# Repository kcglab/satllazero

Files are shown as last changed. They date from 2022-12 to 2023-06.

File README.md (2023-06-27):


DOI (https://doi.org/10.21105/joss.05147)

# Overview
**SATLLA-0**, also known as satllazero, is an open-source project that aims to develop a fully functional pico-satellite. The project includes both the software and hardware of the pico satellite, as well as a ground station. The goal of the project is to enable any science class (in high school or university) to experience the "new space" at a fraction of the price of existing solutions.

# Our Vision
The SATLLA-0 project is all about building a fully functional pico-satellite that's based on a design that's already been launched into space (see [SATLLA-2B](https://tinygs.com/satellite/SATLLA-2B)). Researchers and 12K students can get involved, and the project includes the software, hardware, and ground station you need to make it happen. The goal is to make it possible for any science class to experience the "new space" without breaking the bank.

<div style="display: flex; justify-content: center;">
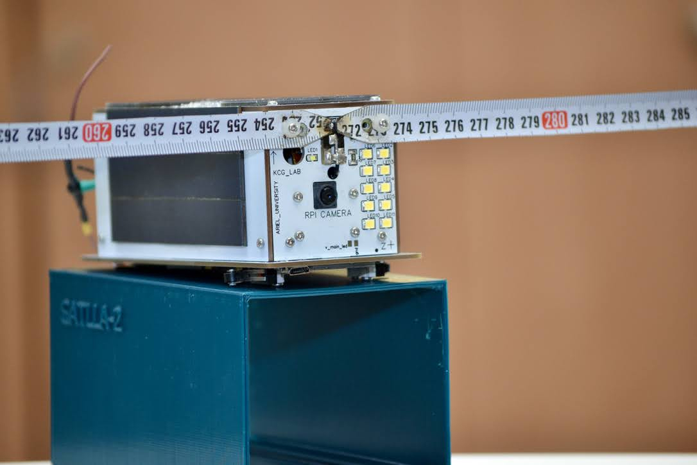
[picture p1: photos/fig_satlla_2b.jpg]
SATLLA-2B
  
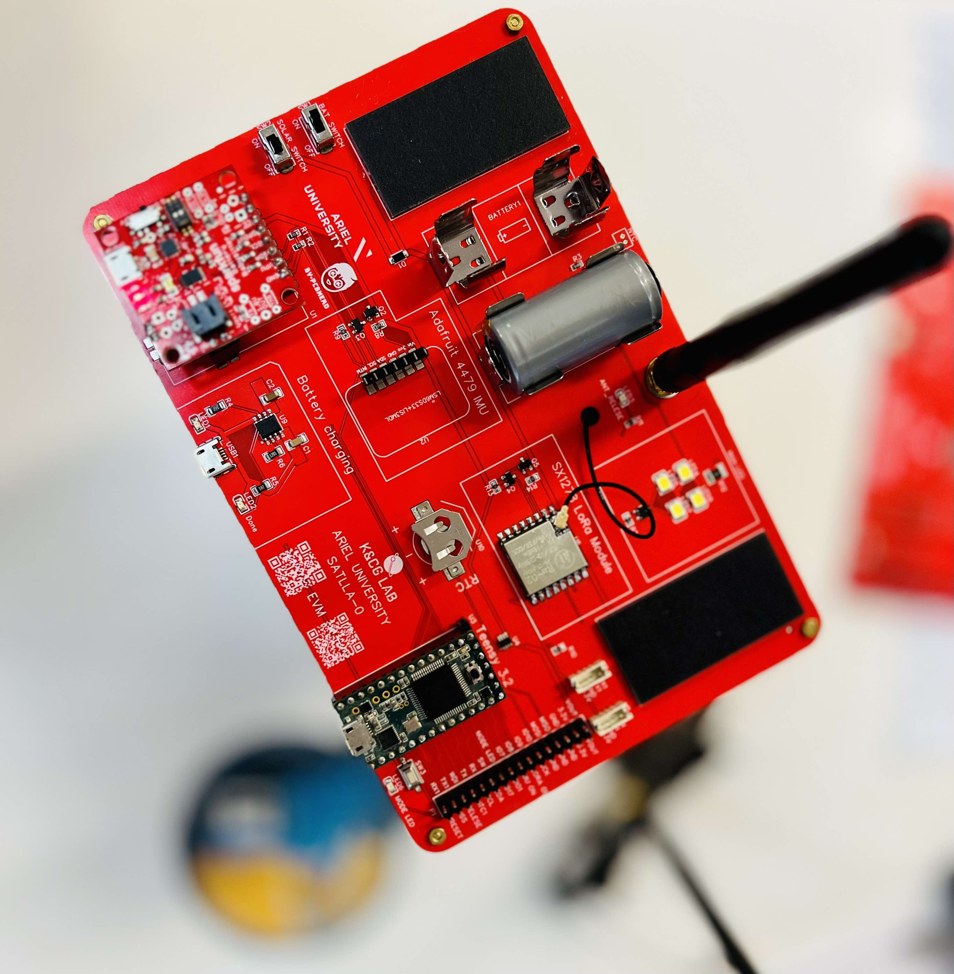
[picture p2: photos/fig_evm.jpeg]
SATLLA-0 EVM Board
  
</div>

## Table of contents

- [Description](#description)
- [What's included](#whats-included)
- [Features](#features)
- [Features](#Features)
- [Supported Hardware](#supported-Hardware)
- [SATLLA-0 EVM Board](#satlla-0-evm-board)
- [Installation](#installation)
- [For more info](#for-more-info)
- [Bugs and feature requests](#bugs-and-feature-requests)
- [Copyright and license](#copyright-and-license)
- [Links](#links)
- [Citation](#citation)

## Description
The SATLLA-0 core flight system is an open-source flight software that is used by the SATLLA-2B satellite. The library was designed to be a starting point for academic institutions and schools that want to build or experiment with a laboratory or functional nanosatellite. The system has three main components: the Master, the on-board computer, and the Ground Station. For more information on each component, please see the following section. The main library contains the satellite's flight software, written in Arduino. Arduino is a C/C++ based programming language that is open source and easy to learn. This library was developed for the Teensy 3.x/4.x microcontroller family, which is the main microprocessor unit (MPU) of the SATLLA-2B nanosatellite. However, the library can be compiled for other microcontrollers using the definitions available in the library.

## What's included
The repo is structured as follows:
+ software: The flight software is divided into three sub-folders:
  + SAT0_Ground: The ground station module written in Arduino [SAT0_Ground](/software/SAT0_Ground).
  + SAT0_Master: The satellite main computer module written in Arduino [SAT0_Master](/software/SAT0_Master)
  + SAT0_OBC: The on-board computer (OBC) module written in Python [SAT0_OBC](/software/SAT0_OBC).
+ hardware: Contains the hardware schematics of the satellite.
+ MD: Contains MD files describing the satellite commands, beacons and bill of materials (BOM).
+ stl: Contains 3D sketches.
+ paper: Contains the JOSS submission paper.

The SATLLA-0 libraries offer the ability to be used independently, meaning that each library component may be utilized separately according to the user's specific requirements. For instance, the SAT0_MASTER satellite flight software can be integrated with alternate ground station software. However, it is essential to know that adjustments relating to radio frequencies and message structures are needed.

## Features
The SATLLA-0 flight software platform includes the following key features:
+ A functional nanosatellite based on a Teansy microcontroller which supports the following subsystems: 
  + 2P structure.
  + Electrical Power System (EPS).
  + Telecommand and communications based on LoRa UHF and S-band. 
  + GPS.
  + Inertial Measurement Unit (IMU).
  + Thermistors (Temperature).
  + High-power array LED.
+ An on-board computer (OBC) for research activities based on a RaspberryPi Zerro.
  + Linux-based 
  + Integrated camera.
  + Variety of payloads including Attitude Determination and Control System (ADCS) based on reaction wheels, an Automatic Dependent Surveillance-Broadcast (ADS-B) receiver for surveillance aircraft.
+ A functional ground station based on an ESP32 board.

## Supported Hardware
A list of all the hardware required to assemble a functional nanosatellite is available [here](/MD/bom.MD).
The following boards are being used in this repository:
+ SAT0_Ground: WiFi LoRa ESP32 from Heltec or TTGO.
+ SAT0_Master: Teensy 3.6/4.1 microcontroller.
+ SAT0_OBC: RPI-Zero or RPI-Zero-W.

## SATLLA-0 EVM Board
The SATLLA-0 evaluation board is specifically designed for flat CubeSats, offering a comprehensive platform for testing and experimenting with various satellite functionalities. This evaluation board incorporates a wide range of satellite sensors, enabling researchers and engineers to assess and explore the full capabilities of the SATLLA-0 system. By providing access to most of the essential sensors used in satellites, the board allows for in-depth evaluation and analysis of different aspects, such as thermal management, power optimization, and communication protocols.
Please refer to [EVM_BOARD](/hardware/evm_board) for more details.

## Installation
SATLLA-0 is written in Arduino, and can be installed via Arduino, Teensyduino or any other IDE supporting Arduino.
Please refer to [wiki](https://github.com/kcglab/satllazero/wiki) for details installation.

## For more info
For more into on SATLLA-0, its workings, inputs, outputs and more see the [wiki](https://github.com/kcglab/satllazero/wiki).

## Bugs and feature requests
Please submit bug reports and feature requests to the issue tracker on GitHub: [SATLLA-0 issue tracker](https://github.com/kcglab/satllazero/issues)

## Copyright and license
This program is released as open source software under the terms of [GPL3 License](https://github.com/kcglab/satllazero/blob/main/LICENSE).

## Links
1. A great place to learn more on SATLLA project: [SATLLA Channel](https://www.youtube.com/watch?v=bJ7NgBDLjMQ)
2. SATLLA 2 DIY KIT Assembly [iFixIt Build Instructions](https://www.ifixit.com/Guide/SATLLA+2+DIY+KIT+Assembly/147004)
3. A good starting point is to use a Weather Balloons: [Extreme Long-RAnge Wi-Fi](https://www.youtube.com/watch?v=0xc7XjHUJkM&t=41s)

## Citation
If you'd like to cite us in a project or publication, please include a reference to the JOSS paper:
```
@article{Ronen_SATLLA0_A_Flight_2023,
  author = {Ronen, Rony and Britvin, Michael and Moshe, Boaz Ben},
  doi = {10.21105/joss.05147},
  journal = {Journal of Open Source Software},
  month = jun,
  number = {86},
  pages = {5147},
  title = {{SATLLA0: A Flight Software Platform for Aerospace and STEM Education}},
  url = {https://joss.theoj.org/papers/10.21105/joss.05147},
  volume = {8},
  year = {2023}
}
```

Ariel University. 2023.

## Troubleshoot
* Issue w/Actions

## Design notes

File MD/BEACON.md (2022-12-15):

# SATLLA0 Decode Long Beacon:

## Description:
SATLLA0 has long and short beacons. Each beacon is sent in a period of 45 seconds to 1 minute depends on the battery power.

## Short Beacon:
- Short beacon consists of 12  bytes:
> uint8_t local_address;   // 1, SAT Address/Call Sign \
> uint8_t sd_outbox;       // 2, Pending files to sent \
> uint8_t msg_type;        // 3, Message Type per messgae_type_e enum \
> uint8_t msg_received;    // 4, Recevied Messages \
> uint16_t msg_index;      // 5, Message ID \
> uint16_t battery_volts;  // 6, Read battery voltage (mV) \
> int16_t battery_current; // 7, Read average current (mA) \
> int8_t sns_ntc1;         // 8, Temperature \
> int8_t sns_ntc2;         // 9, Temperature \

## Long Beacon:
- Long beacon consists of a header (9 bytes) and payload (dynamic size).
- The type of the beacon located in the 3rd byte of the message.
- SATLLA0 has messages that aren't beacons. Nevertheless, all of them has the same structure: 9 byte header and rest is payload.
- The header is as follows:
- lora_data_t:
> uint8_t local_address; // 1, SAT Address/Call Sign. \
> uint8_t destination;   // 2, Ground Station address \
> uint8_t msg_type;      // 3, Message Type per messgae_type_e enum \ 
> uint8_t msg_size;      // 4, Message Length (for payload) \
> uint16_t msg_index;    // 5, Message ID \
> uint16_t msg_time;     // 7, The time of the message since last boot \
> uint8_t msg_ack_req;   // 9. Message ack req. 0=False. 1=True \
> uint8_t msg_payload[]; // 10. The Data \

- The payload structure in a long beacon consists of 52 bytes as follows:
-- gps_data_t (include date_time_t) 20 bytes
-- sns_data_t 16 bytes
-- battery_data_t 12 bytes
-- sd_data_t 4 bytes

- gps_data_t:
> date_time_t gps_date_time; // 1, Date/Time \
> float gps_lat;        // 2, Latitude \
> float gps_lng;        // 3, Longitude \
> uint16_t gps_alt;     // 4, Altitude \
> uint16_t gps_speed;   // 5, Sat Speed KPH \
> uint16_t gps_course;  // 6, Sat Course Degree \
> uint8_t gps_sat;      // 7, Number of gps satellites \

-date_time_t:
> uint8_t gps_month; // 1, Month \
> uint8_t gps_day;   // 2, Day \
> uint8_t gps_hour;  // 3, Hour \
> uint8_t gps_min;   // 4, Min \

- sns_data_t:
> int16_t sns_gx;         // 1, Gyro X rad/s \
> int16_t sns_gy;         // 2, Gyro Y rad/s \
> int16_t sns_gz;         // 3, Gyro Z rad/s \
> int16_t sns_mx;         // 4, Mag X uTesla \
> int16_t sns_my;         // 5, Mag Y uTesla \
> int16_t sns_mz;         // 6, Mag Z uTesla \
> int16_t sns_bmp_temp_c; // 7, Temperature C \
> int8_t sns_ntc1;        // 8, ? Temperature 1 C \
> int8_t sns_ntc2;        // 9, ? Temperature 2 C \

- battery_data_t
> int8_t battery_soc;             // 1, Read state-of-charge (%) \
> int8_t battery_health;          // 2, Read state-of-health (%) \
> uint16_t battery_volts;         // 3, Read battery voltage (mV) \
> int16_t battery_current;        // 4, Read average current (mA) \
> uint16_t battery_full_capacity; // 5, Read full capacity (mAh) \
> uint16_t battery_capacity;      // 6, Read remaining capacity (mAh) \
> int16_t battery_power;          // 7, Read average power draw (mW) \

- sd_data_t:
> uint8_t sd_outbox; // 1, Pending files to upload \
> uint8_t sd_sent;   // 2, Files sent \
> uint8_t sd_rpi;    // 3, Pending files under Mission Computer to upload \
> uint8_t sd_files;  // 4, All files on the SD - Informative. \

- enum messgae_type_e:
> type_becon = 0x00 \
> type_echo = 0x01 \
> type_ack = 0x02 \
> type_range = 0x03 \
> type_rpi = 0x04 \
> type_text = 0x05 \
> type_sbeacon = 0x06 \
> type_command = 0x07 \
> type_setting = 0x08 \
> type_none = 0x09 \
> type_mv = 0x0A \
> type_ld = 0x0B \
> type_rng = 0x0C \

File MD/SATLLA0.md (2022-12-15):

# SATLLA0 Code

## 1. Setup
- 1.1 RTC
- 1.2 SPI Pin: 13 or 14 (Based on Teensy)
- 1.3 Wire
- 1.4 Watchdog
- 1.5 SD Card
- 1.6 Flash FS
- 1.7 Mode Led
- 1.8 Main LED
- 1.9 Laser Setup
- 1.10 EEPROM
- 1.11 IMU (BNO or LSM)
- 1.12 LoRa 433
- 1.13 LoRa 2.4
- 1.14 GPS
- 1.15 NTC (1 and 2)
- 1.16 Babysitter (BQ27441)
- 1.17 Initial Boot (Antenna Deploy)
- 1.18 Increase Reset index

## 2. Main Loop
- 2.1 WD Heartbeat
- 2.2 Read Babysitter Func
- 2.3 Check Battery Status Func 
- 2.4 Set satellite mode Func (Based on battery status)
- 2.5 If state is higher than panic, then:
- 2.5.1 If 1 minute passed from last beacon, then:
- 2.5.1.1 Set Short/Long beacon (Based on battery status and at least 5 long every hour)
- 2.5.1.2 Prepare Beacon parameters Func
- 2.5.1.3 Send Beacon using LoRa 433
- 2.5.1.4 Wait one second
- 2.5.1.5 Send Beacon using LoRa 2.4 (If loRa 2.4 is On - Depends on Satellite health)
- 2.6 Smart wait for 20 seconds (Listen to commands)
- 2.7 Handle Tasks Func (Auto and based on commands received)
- 2.8 If not in mission
- 2.8.1 If GFSK is allowed and state is higher than panic, then:
- 2.8.1.1 Switch modem to GFSK 433
- 2.8.1.2 Send beacon using GFSK 433
- 2.8.1.3 Switch back to LoRa 433
- 2.8.2 If in panic mode, then
- 2.8.2.1 Sleep for 45 seconds
- 2.8.2.2 Else, Sleep for at most 15 seconds (Depends on last beacon sent time)

## 3. Smart Delay Func
- 3.1 Loop for period
- 3.1.1 If GPS is on, feed GPS
- 3.1.2 If received 433, break
- 3.1.3 If received 2.4, break
- 3.1.4 WD Heartbeat
- 3.2 If break, handle message (2.4 or 433)
- 3.3 If restart requested, wait 2 seconds and restart.

## 4. Sleep Delay Func
- 4.1 Loop for period
- 4.1.1 If IMU is On and Not Sleep, Sleep
- 4.1.2 If LoRa 433 is On and Not Sleep, Sleep
- 4.1.3 If Lora 2.4 is On and Not Sleep, Sleep
- 4.1.4 If GPS is On and Not Sleep, Sleep
- 4.1.5 WD Heartbeat
- 4.2.1 If IMU is On and Sleep, Resume
- 4.2.2 If LoRa 433 is On and Sleep, Resume
- 4.2.3 If Lora 2.4 is On and Sleep, Resume
- 4.2.3 If GPS is On and Sleep, Resume
- 4.1.6 WD Heartbeat

## 5. Satellite Health Func
- 5.1 Switch Satellite State
- 5.1.2 Case: Panic power
- 5.1.2.1 If GPS is On, then turn Off
- 5.1.2.2 If IMU is On, then turn Off
- 5.1.2.4 If LoRa 433 is On, then turn Off
- 5.1.2.5 If LoRa 24 is On, then turn Off
- 5.1.3 Case: Medium power
- 5.1.3.1 If GPS is On, then turn Off
- 5.1.3.2 If IMU is Off, then turn On
- 5.1.3.4 If LoRa 433 is Off, then turn On
- 5.1.3.5 If LoRa 24 is Off, then turn On
- 5.1.3 Case: High power
- 5.1.3.1 If GPS is Off, then turn On
- 5.1.3.2 If IMU is Off, then turn On
- 5.1.3.4 If LoRa 433 is Off, then turn On
- 5.1.3.5 If LoRa 24 is Off, then turn On

## 6. Switch Beacon Type Func
- 6.1 If Satellite state > Medium power, then
- 6.1.2 Use Long Beacon
- 6.1.3 Else, Use Short Beacon
- 6.1.4 In addition, If last sent long beacon > 1 hour, then 
- 6.1.4.1 Use Long Beacon for the next 5 messages

## 7. Handle Beacon Func:
- 7.1 Read Babysitter
- 7.2 Read IMU
- 7.3 Read NTC
- 7.4 Read GPS
- 7.5 If SD, then list files
- 7.6 If SD error or SD overwrite, then list files from FS
- 7.7 Add Infodata to beacon
- 7.8 Add Metadata to beacon 
- 7.9 Prepare Long/Short beacon

## 8. Send Beacon Func:
- 8.1 If Stop Flag raised, return
- 8.2 Send Short/Long beacon via LoRa 433/24
=======
1.1 RTC
1.2 SPI Pin: 13 or 14 (Based on Teensy)
1.3 Wire
1.4 Watchdog
1.5 SD Card
1.6 Flash FS
1.7 Mode Led
1.8 Main LED
1.9 Laser Setup
1.10 EEPROM
1.11 IMU (BNO or LSM)
1.12 LoRa 433
1.13 LoRa 2.4
1.14 GPS
1.15 NTC (1 and 2)
1.16 Babysitter (BQ27441)
1.17 Initial Boot (Antenna Deploy)
1.18 Increase Reset index

## 2. Main Loop
2.1 WD Heartbeat
2.2 Read Babysitter Func
2.3 Check Battery Status Func 
2.4 Set satellite mode Func (Based on battery status)
2.5 If state is higher than panic, then:
2.5.1 If 1 minute passed from last beacon, then:
2.5.1.1 Set Short/Long beacon (Based on battery status and at least 5 long every hour)
2.5.1.2 Prepare Beacon parameters Func
2.5.1.3 Send Beacon using LoRa 433
2.5.1.4 Wait one second
2.5.1.5 Send Beacon using LoRa 2.4 (If loRa 2.4 is On - Depends on Satellite health)
2.6 Smart wait for 20 seconds (Listen to commands)
2.7 Handle Tasks Func (Auto and based on commands received)
2.8 If not in mission
2.8.1 If GFSK is allowed and state is higher than panic, then:
2.8.1.1 Switch modem to GFSK 433
2.8.1.2 Send beacon using GFSK 433
2.8.1.3 Switch back to LoRa 433
2.8.2 If in panic mode, then
2.8.2.1 Sleep for 45 seconds
2.8.2.2 Else, Sleep for at most 15 seconds (Depends on last beacon sent time)

## 3. Smart Delay Func
3.1 Loop for period
3.1.1 If GPS is on, feed GPS
3.1.2 If received 433, break
3.1.3 If received 2.4, break
3.1.4 WD Heartbeat
3.2 If broken, handle message (2.4 or 433)
3.3 If restart requested, wait 2 seconds and restart.

## 4. Sleep Delay Func
4.1 Loop for period
4.1.1 If IMU is On, Sleep
4.1.2 If LoRa 433 is On, Sleep
4.1.3 If Lora 2.4 is On, Sleep
4.1.4 If GPS is On, Sleep
4.1.5 WD Heartbeat

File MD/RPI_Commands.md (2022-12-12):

# RPI Commands Code and Examples
- Commands are sent in Hex
- Structure: <SATID><CMD><PARAMS>

## CMD_RPI_1_COMMAND 0x55       // RPI Command
## CMD_RPI_1_COMMAND_X_MNT 0x56 // RPI turn on in X minutes command
- Sending command to RPI is either 0x55 or 0x56 if delay is required.

## CMD_POWER_ON 0x03 (Power On)
- RPI power on.
- Params: N/A
- B45503
- 
## CMD_TAKE_PHOTO 0x04
- RPI Take photo - old method.
- Params: Width: (100), Mode: (1) = Day, 2 = Night,
- B45504

## CMD_SIT 0x05 (Satellite Image Transfer)
- RPI Take photo - new method.
- Params: N/A
- B45505

## CMD_SEEK_LASER 0x06 (Satellite Image Transfer)
- RPI Take photo - new method.
- Params: Freq: (2.0), Threshold: (1.0), Timeout: (45) secs
- B45506

## CMD_RWCS 0x07 (Reaction Wheel Control System)
- RPI Attitude Determination and Control System (ADCS)
- Params: desiredAngleX, Y, Z: (0), Timeout: (1) min
- B45507

## CMD_POWER_OFF 0x08 (Power Off)
- RPI power off.
- Params: N/A
- B45508

## CMD_DROP_OUTBOX 0x09 (Clear Outbox folder)
- RPI Clear Outbox folder.
- Params: N/A
- B45509

## CMD_ADSB 0x0E ()
- RPI ADS-B Exchange
- Params: N/A
- B4550E

## CMD_NEW_TAKE_PHOTO 0x0F ()
- RPI Take Photo - new experimental was
- Params: missionType: (0), quality: (0), iso: (0)(2b), shutter (0)(2b), width: (0)(2b), height: (0)(2b) 
- B4550F

## DataTypes:
- OTHER = 0  # 0x00
- PHOTO = 1  # 0x01
- META = 20  # 0x14
- STARS = 21  # 0x15
- TEXT = 22  # 0x16
- DATA = 23  # 0x17
- STD_OUT = 24 # 0x18
- STD_ERR = 25 # 0x19
- LASER_TEXT = 26 # 0x1A
- LASER_VIDEO = 27 # 0x1B

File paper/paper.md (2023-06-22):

---
title: 'SATLLA0: A Flight Software Platform for Aerospace and STEM Education'
tags:
  - Python
  - Arduino
  - CubeSat
  - PicoSat
  - New-space
  - Lora
authors:
  - name: Rony Ronen
    orcid: 0000-0002-1300-5236
    affiliation: "1"
  - name: Michael Britvin
    orcid: 0009-0003-5492-4014
    affiliation: "2"
  - name: Boaz Ben Moshe
    orcid: 0000-0002-1580-5421
    affiliation: "1"
affiliations:
  - name: School of Computer Science, Ariel University, 47100, Israel
    index: 1
  - name: Faculty of Engineering, Ariel University, 47100, Israel
    index: 2
date: 19 December 2022
bibliography: paper.bib
---
# Summary
Nanosatellites are becoming a preferred platform for testing innovative technologies and conducting academic research in space. Flight Software (FSW) is a software program that operates on a processor embedded within the satellite structure [@miranda2019comparative]. It assumes the crucial responsibility of managing various aspects of satellite operations, including activity control, data processing, and ensuring satellite health and safety. By fulfilling these tasks, the FSW empowers the satellite to execute all actions essential for achieving its scientific objectives.

[SATLLA-0](https://github.com/kcglab/satllazero) is an open-source platform designed for academic institutions and school students to build and explore laboratory nanosatellites. It is based on the flight software utilized by the [SATLLA-2B](https://tinygs.com/satellite/SATLLA-2B) nanosatellite, which was developed and constructed by the Nanosatellite Research Laboratory of Ariel University. The successful launch of the SATLLA-2B nanosatellite took place on January 13, 2022, aboard a Falcon 9 launch vehicle. Since its launch, SATLLA-2B has been operating seamlessly, with its transmissions being received daily by a wide range of users on tinyGS.com.

SATLLA-0 is divided into three main libraries, with the main library, [SAT0_Master](../software/SAT0_Master), responsible for the ongoing operation of the satellite, the [SAT0_OBC](../software/SAT0_OBC) library responsible for the operation of the satellite's research objective, and the [SAT0_Ground](../software/SAT0_Ground) library responsible for transmitting telecommand to the satellite and receiving satellite transmissions and routing the data for further analysis.

# Statement of need
Building a nanosatellite and developing flight software is challenging for newcomers to the space (i.e., new-space) field due to the lack of literature and high cost. There are open-source frameworks for space projects developed by space agencies, universities, or commercial companies to serve as reference designs and encourage code reuse in their future projects [@jamie2017basic]. These frameworks have not yet gained significant adoption outside of their host organizations [@miranda2019comparative] for the following reasons:

* Flight software is tailored to a satellite of a specific design and is not transferable to another design.
* Flight software is not based on open source software or the entire flight software has not been released as open source software.
* Flight software is too complicated and may not be suitable for organizations just starting out or for STEM education.

At the same time, using an existing software framework leads to a shorter development program at lower costs and better quality. These effects are beneficial for organizations such as universities or schools that want to enter the space field. These reasons have led us to release the SATLLA-2B flight software as open-source code with additional documents to build a nanosatellite.

# Description
The SATLLA-0 core flight system serves as open-source flight software utilized by the SATLLA-2B satellite. Its purpose is to provide a foundational framework for academic institutions or schools interested in constructing or experimenting with laboratory or functional nanosatellites. As previously mentioned, this system comprises three distinct components. The primary library encompasses the satellite's flight software, employing the Arduino programming language, which is based on C/C++, renowned for its open-source nature and ease of comprehension. The primary focus during the development of the main library was to cater to the specific requirements of the Teensy 3.x/4.x microcontroller family, which functions as the central microprocessor unit (MPU) for the SATLLA-2B nanosatellite. However, it is worth noting that the library incorporates accessible definitions that enable the compilation of the library for alternative microcontrollers, expanding its compatibility beyond the Teensy series.

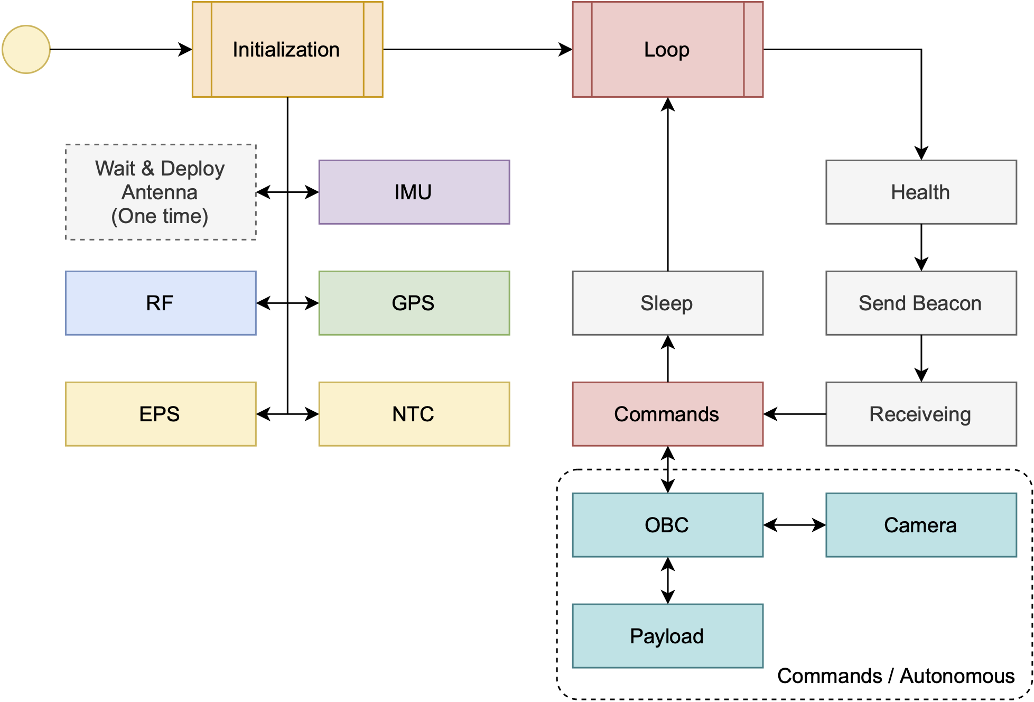
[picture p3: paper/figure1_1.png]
SATLLA-0 FSW two main states: Initialization and Operation.\label{fig:figure1_1}


The FSW consists of two primary states, as deduced from the system requirements of a state machine [@gonzalez2019architecture] (\autoref{fig:figure1_1}).

* **Initialization**: During the initialization phase, the FSW undertakes the initial configuration process by accessing the initialization parameters stored in the flash memory of the MCU. Upon the initial startup or following a complete reset, the FSW utilizes predefined default values. Simultaneously, this state encompasses the initialization of different satellite modules, such as the IMU, GPS, and communication systems. Subsequently, the satellite's state is evaluated to ascertain the operational mode, which can be categorized as Panic, Reduced Operation, or Normal Operation.

* **Operation**: After concluding the initialization state and establishing the operational mode, the FSW proceeds to enter iterative loops. These loops enable the FSW to query the diverse modules and sensors, subsequently responding appropriately to the received data. Additionally, the FSW periodically transmits a heartbeat signal to the watchdog, ensuring it does not reach a critical state. This proactive measure of sending regular heartbeats prevents the watchdog from reaching a zero point or malfunctioning.

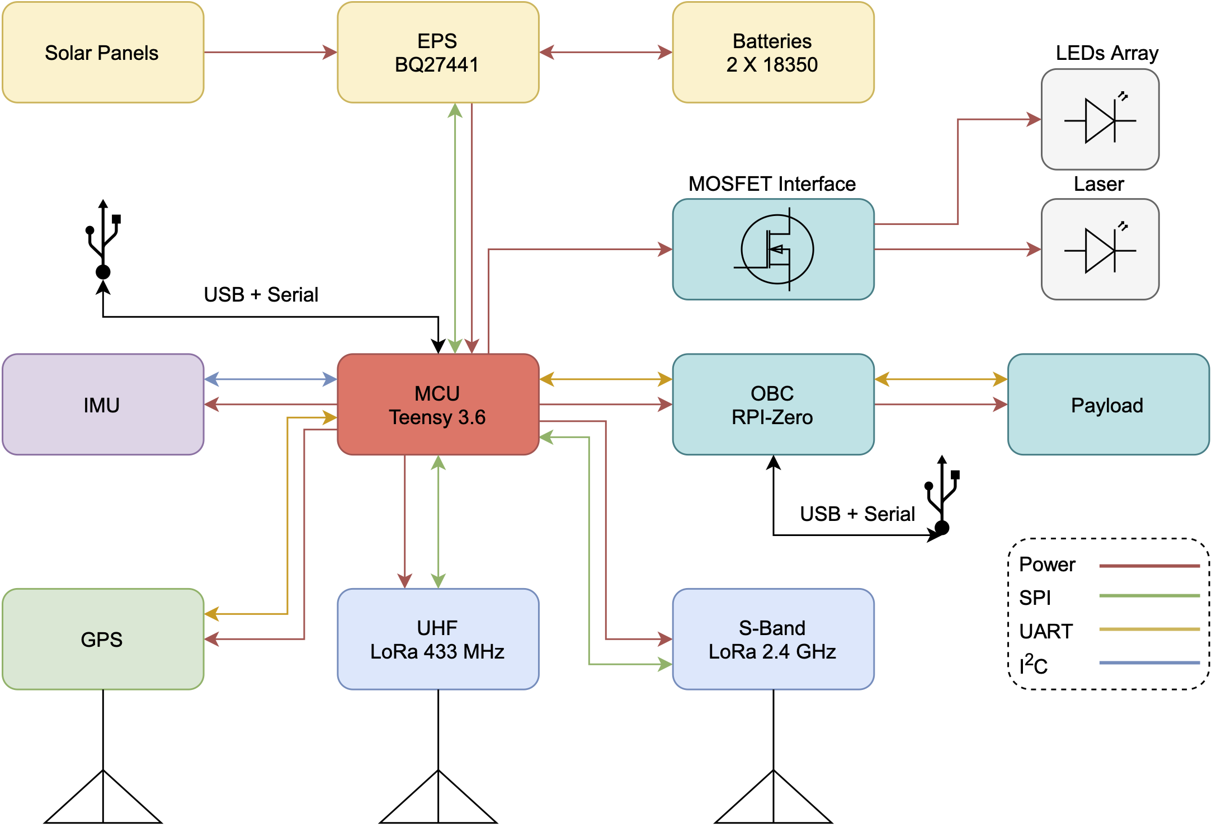
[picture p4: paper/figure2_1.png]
SATLLA-0 Power and Protocol interfaces.\label{fig:figure2_1}


A technical overview of the power, data, and RF interfaces used in the SATLLA-0 system is available in \autoref{fig:figure2_1}. The specific interface used for each component is determined by the communication type integrated into that particular component. Some components possess multiple communication interfaces, such as Integrated Communications (I2C), Serial Peripheral Interface (SPI), or Universal Asynchronous Receiver Transmitter (UART). In such cases, the preferred communication type is selected based on the component's requirements. For example, both the On-Board Computer (OBC) and the GPS module communicate with the microcontroller unit (MCU) using a UART interface. This approach ensures the MCU remains operational while collecting necessary data. Additionally, the power supply interface regulates voltage levels (3.3 V) for the satellite's avionics and payloads.

For a full documentation of `SATLLA-0`, the reader is referred to our [GitHub page](https://github.com/kcglab/satllazero).

# Acknowledgement
The authors acknowledge the great work and dedication of the entire SATLLA team and the support of the Department of Computer Science at Ariel University. Special thanks are extended to the students who participated in the mission design for the nanosatellite: Zachi Ben-Shitrit, Assaf Chia, Shaya Sonnenberg, Shai Aharon, Michael Twito, Revital Marble, and Aharon Got. This work has been partially supported by the Ariel Cyber Innovation Center.

# References

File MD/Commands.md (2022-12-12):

# Commands Code and Examples
- Commands are sent in Hex
- Structure: <SATID><CMD><PARAMS>

## CMD_CPU_RESTART 0x01
- Restart Satellite
- B401

## CMD_RST_GPS 0x02
- Reset GPS
- B402

## CMD_RST_IMU 0x03
- Reset IMU
- B403

## CMD_RST_SETTING 0x04
- Reset global setting
- B404

## CMD_RST_OUTBOX 0x05
- Delete OUTBOX folder
- B405

## CMD_RST_SENT 0x06
- Delete SENT folder
- B406

## CMD_RST_SD_CARD 0x07
- Wipe SD Card (Format)
- B407

## CMD_RST_OPER_TIME 0x08
- Reset the operation time counter
- B408

## CMD_RST_FULL 0x09
- Wipe SD CARD and EEPROM (Format and Delete EEPROM settings)
- B409

## CMD_STRT_BLINK 0x0A
- Start Blink LED
- B40A

## CMD_STRT_BLINK_X_MNT 0x0B
- Start Blink LED in X minutes
- Params: X = 2 bytes
- B40B0168 Blink in 360 minutes (0x168 = 360)

## CMD_SEND_BEACON_433 0x0C
- Send long beacon on 433 now
- B40C

## CMD_SEND_BEACON_24 0x0D
- Send long beacon on 24 now
- B40D

## CMD_GET_LOG_LN 0x0E
- Send a line from the log file. Default is first line and LoRa 433
- Params: Line No = 2 bytes, Radio = 1 byte
- B40E000100

## CMD_ECHO_MESSAGE 0x0F
- Echo Message
- Params: Radio = 1 byte, Repeat = 1 byte, Message = Upto 225 bytes
- B40F0001020304

## CMD_ECHO_MESSAGE_X_MNT 0x25
- Echo Message in X minutes
- Params: Radio = 1 byte, X = 2 bytes, Repeat = 1 byte, Message = Upto 223 bytes
- B42501A00102030405

## CMD_FAT_ON_OFF 0x10             // FAT on/off
- Open/Close FAT Module
- Params: FAT Module = 1 byte, Off/On = 1 byte (0/1)
- B4100301

## CMD_CHG_SETTING 0x11            // Change one global setting. Index, Value
- Change gloval setting param by index
- Params: Index = 1 byte, Value = 1 byte

## CMD_GET_SETTING 0x12            // Get global setting
- Get global setting

## CMD_CHG_GLB_SET 0x13            // Change entire global setting
- Change Global Settings
- Params: setting_data_g

## CMD_STOP_TX_FLAG 0x14           // A request to stop TX
- Stop beacon transmitting

## CMD_RESUME_TX_FLAG 0x15         // A request to resume TX
- Resume beacon transmitting

## CMD_DEPLOY_ANT 0x16             // A request to deploy antenna
- Deploy antenna. Keep the FAT open for X seconds.
- Params: Seconds = 1 byte

## CMD_STRT_BLINK_LED_LSR 0x17     // Blink both LED and laser
- Blink both, LED and Laser

## CMD_GET_META 0x18               // Retrieve a specific meta
- Get metafile
- Params: Mission = 2 bytes, Radio = 1 byte
- 

## CMD_GET_FILE_PART 0x19          // Retrieve a file by mission and index and part #
- Get file part
- Params: Mission = 2 bytes, File Index = 2 bytes, Packet Length = 1 byte, Part Number = 1 byte, Radio = 1 byte

## CMD_GET_FILE 0x1A               // Retrieve a file by mission and index
- Get file
- Params: Mission = 2 bytes, File Index = 2 bytes, Packet Length = 1 byte, Radio = 1 byte

## CMD_GET_LAST_FILE 0x1B          // Retrieve last meta
- Get last meta file created 
- Params: Radio = 1 byte

## CMD_GET_OUTBOX 0x1C             // Retrieve OUTBOX folder/Meta Files
- Get all meta files from Outbox folder
- Params: Radio = 1 byte

## CMD_GET_SENT 0x1D               // Retrieve SENT folder/Meta files that were sent
- Get all meta files from Sent folder
- Params: Radio = 1 byte

## CMD_SET_LORA_433_BSCP 0x1F      // Set LoRa 433
## CMD_SET_LORA_24_BSCP 0x20       // Set Lora 24
## CMD_RANGING_SLAVE_24 0x21       // Set SAT into SLAVE for ranging 24
## CMD_STRT_BLINK_LSR 0x22         // Start Blink Laser
## CMD_STRT_BLINK_X_MNT_LSR 0x23   // Start Blink Laser in X minutes
## CMD_RANGING_RUN 0x24            // Start Master Ranging Execution
## CMD_RANGING_CALIB 0x26          // Set SAT into SLAVE for ranging 24 calibration
## CMD_SET_DATE_TIME 0x27          // Set a Date and Time
## CMD_RST_DATE_TIME 0x28          // Reset Date and Time to last burn time date
## CMD_SEND_BEACON_FSK 0x29        // Send Beacon on 433 now
## CMD_SET_LORA_433_BW 0x2A        // Set Lora 433 BW
## CMD_SET_LORA_433_SF 0x2B        // Set Lora 433 SF
## CMD_SET_LORA_433_CR 0x2C        // Set Lora 433 CR
## CMD_SET_LORA_433_PM 0x2D        // Set Lora 433 PM
## CMD_SET_LORA_433_PL 0x2E        // Set Lora 433 PL
## CMD_SET_LORA_433_LDRO 0x2F      // Set Lora 433 LDRO
## CMD_SET_LORA_433_CRC 0x30       // Set Lora 433 CRC
## CMD_SET_LORA_433_OFFSET 0x3D    // Set Lora 433 Offset
## CMD_SET_LORA_433_FREQUENCY 0x3F // Set Lora 433 Frequency
## CMD_SET_LORA_433_STRUCT 0x40    // Set Lora 433 Struct
## CMD_SET_LORA_433_SW 0x3A        // Set Lora 433 SW
## CMD_SET_FSK_433_BW 0x31         // Set FSK 433 BW
## CMD_SET_FSK_433_SF 0x32         // Set FSK 433 SF
## CMD_SET_FSK_433_CR 0x33         // Set FSK 433 CR
## CMD_SET_FSK_433_PM 0x34         // Set FSK 433 PM
## CMD_SET_FSK_433_PL 0x35         // Set FSK 433 PL
## CMD_SET_FSK_433_LDRO 0x36       // Set FSK 433 LDRO
## CMD_SET_FSK_433_CRC 0x37        // Set FSK 433 CRC
## CMD_SET_FSK_433_DS 0x38         // Set FSK 433 DS
## CMD_SET_FSK_433_BR 0x39         // Set FSK 433 BR
## CMD_SET_FSK_433_SW 0x3B         // Set FSK 433 SW
## CMD_SET_FSK_433_DEVIATION 0x3C  // Set FSK 433 Deviation
## CMD_SET_FSK_433_FREQUENCY 0x3E  // Set FSK 433 Frequency
## CMD_SET_FSK_433_STRUCT 0x41     // Set Lora 433 Struct
## CMD_SET_LORA_24_STRUCT 0x42     // Set Lora 433 Struct
## CMD_SET_LORA_24_BW 0x43         // Set Lora 433 BW
## CMD_SET_LORA_24_SF 0x44         // Set Lora 433 SF
## CMD_SET_LORA_24_CR 0x45         // Set Lora 433 CR
## CMD_SET_LORA_24_PM 0x46         // Set Lora 433 PM
## CMD_SET_LORA_24_PL 0x47         // Set Lora 433 PL
## CMD_SET_LORA_24_SW 0x48         // Set Lora 433 SW
## CMD_SET_LORA_24_LDRO 0x49       // Set Lora 433 LDRO
## CMD_SET_LORA_24_CRC 0x4A        // Set Lora 433 CRC
## CMD_SET_LORA_24_OFFSET 0x4B     // Set Lora 433 Offset
## CMD_SET_LORA_24_FREQUENCY 0x4C  // Set Lora 433 Frequency
## CMD_SET_SAVE_TO_FLASH 0x4D      // Set Lora 433 Frequency
## CMD_GET_OUTBOX_FS 0x4E          // Get Outbox folder from FS
## CMD_GET_SENT_FS 0x4F            // Get Sent folder from FS
## CMD_RST_FS 0x60   // Wipe FS 
## CMD_RST_OPER_TIME_FS 0x61   // Reset the oper time FS

## CMD_RPI_1_COMMAND 0x55       // RPI Command
## CMD_RPI_1_COMMAND_X_MNT 0x56 // RPI turn on in X minutes command

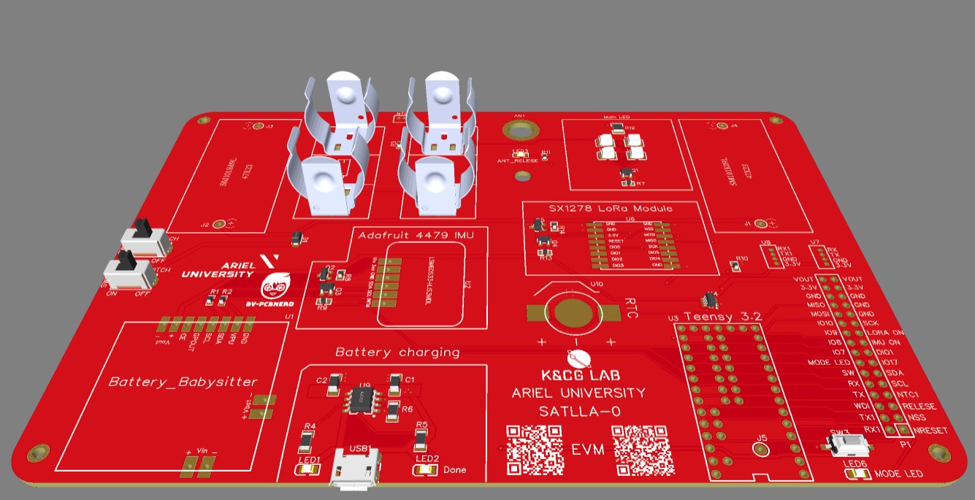
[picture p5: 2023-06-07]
hardware/evm_board/SATLLA_0_EVM_Board.jpeg

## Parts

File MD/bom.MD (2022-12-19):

# SATLLA-0 BOM

Bill of Material of SATLLA-0:

| ID  | Item | Qty | Part | Short | URL |
|-----|---|-----|---|---|---|
| 1 | PCB (External) | 6 | | PCB manufactured by EasyEDA | https://easyeda.com/ |
| 2 | PCB (Internal) | 2 | | PCB manufactured by EasyEDA | https://easyeda.com/ |
| 3 | Teensy 3.6/4.1 | 1 | | Teensy 3.6/4.1 microcontroller | https://www.pjrc.com/store/teensy36.html |
| 4 | RPI-Zero or RPI-Zero-W | 1 | | Raspberry Pi Zero tiny computer | https://www.raspberrypi.com/products/raspberry-pi-zero/ |
| 5 | Dragon-Link antenna | 1 | | A VHF antenna for 433 MHz radio using meter | http://www.fpvpro.com/dragon-link-receiver-antenna-15-cm |
| 6 | LoRa 433 | 1 | | Ra-02 LoRa Module | http://www.ai-thinker.com/pro_view-57.html |
| 7 | LoRa 2.4 | 1 | | LoRa1280 and LoRa1281 strictly uses lead-free process for production and testing, and meets RoHS and Reach standards. | https://www.nicerf.com/products/detail/2-4ghz-lora-wireless-transceiver-module-lora1280-lora1281.html |
| 8 | IMU LSM6DS33+LIS3MDL | 1 | | The board includes an LSM6DS33, a 6-DoF IMU accelerometer + gyro and a LIS3MDL 3-axis magnetometer that can sense where the strongest magnetic force is coming from, generally used to detect magnetic north. | https://www.adafruit.com/product/4485 |
| 9 | RPI Camera v2.1 (No IR) | 1 | | Camera Module v2 | https://www.raspberrypi.com/documentation/accessories/camera.html |
| 10  | Solar Panel 47X23 -> SM101K09L-ND | 6 | | Monocrystalline solar cells | https://ixapps.ixys.com/DataSheet/SM101K09L.pdf |
| 11  | Solar Panel 86X15 -> SM141K08L-ND | 6 | | Monocrystalline solar cells | https://ixapps.ixys.com/DataSheet/SM141K08L.pdf |
| 12  | Meter | 2 | | 14 cm painted meter | |
| 13  | Battery Holder | 4 | | Annealed springs stell with tin nickel plate | https://www.digikey.co.il/en/product-highlight/k/keystone/low-profile-pcb-cylindrical-battery-clips |
| 14  | Micros witch | 2 | | Honeywell MICRO SWITCH standard subminiatures. | https://docs.rs-online.com/dc52/0900766b813c58ae.pdf |
| 15  | Antenna wire 1.1 mm | 2 | | | |
| 16  | Antenna IPEX connector | 1 | | | |
| 17  | Battery Babysitter | 1 | | SparkFun Battery Babysitter - LiPo Battery Manager | https://www.sparkfun.com/products/13777 |
| 18  | 18350 batteries 1200mAh | 2 | P1835C2 | Protected 18350 Li-ion Rechargeable Battery | https://www.keeppower.com.cn/products_detail.php?id=566 |
| 19  | 18350 batteries 1400mAh | 2 | P1835C3 | Protected 18350 Li-ion Rechargeable Battery | https://www.keeppower.com.cn/products_detail.php?id=675 |
| 20  | GPS antenna | 1 | | Antenna Module with Front-End SAW Filter | https://cdn2.taoglas.com/datasheets/AGGBP.SL.18A.07.0060A.pdf |
| 21  | LED | 10  | | Everlight 67-21S/KK4C | https://www.google.com/url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 |
| 22  | External Resistors | 2 | | Use for antenna deploy. | |
| 23  | Mode LED | 1 | | Blinking LED | |
| 24  | JTAG | 12  | | "ZH connector: UL Recognized E60389, CSA Certified LR20812, TUV Certified R9351092, RoHS Compliant" | https://www.jst.co.uk/productSeries.php?pid=106 |
| 25  | USB Socket | 2 | | USB Micro B PC Mount Socket | |
| 26  | Wires | | | JST SH ZH XH PH 1.0mm | |

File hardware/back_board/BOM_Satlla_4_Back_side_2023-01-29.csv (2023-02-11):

ID | Name | Designator | Footprint | Quantity | Manufacturer Part | Manufacturer | Supplier | Supplier Part | Price
1 | 3.3 | R3,R4 | RES-TH_BD4.0-L10.5-P14.50-D0.6 | 2 | RD50T53R3J | TA-I Tech | LCSC | C167570 | 0.002
2 | TS-1092S-B1D2-W | SW1 | SW-SMD_L6.1-W3.6-LS7.9 | 1 | TS-1092S-B1D2-W | Yuandi(台湾元迪) | LCSC | C782859 | 0.01
3 | JST-ZH-2-PIN_HEADER TH | U1,U2 | JST-ZH-2 1.5MM TH | 2

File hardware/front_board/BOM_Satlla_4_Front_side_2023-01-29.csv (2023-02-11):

ID | Name | Designator | Footprint | Quantity | Manufacturer Part | Manufacturer | Supplier | Supplier Part | Price
1 | 67-21S/KK4C-H6565R3R62835Z15/2T | LED2,LED3,LED4,LED5,LED6,LED7,LED8,LED9,LED10,LED11 | LED-SMD_L3.5-W2.8-R-RD | 10 | 67-21S/KK4C-H6565R3R62835Z15/2T | EVERLIGHT | LCSC | C73545 | 0.006
2 | MHT170CRCT | LED12 | LED0805-RD | 1 | MHT170CRCT | MEIHUA | LCSC | C389523 | 0.005
3 | 5 | R2 | R1210 | 1
4 | JST-ZH-2-PIN_HEADER TH | U1,U2 | JST-ZH-2 1.5MM TH | 2
5 | Raspberry Pi Camera Module v2 | U3 | RASPBERRY PI CAMERA MODULE V2 | 1

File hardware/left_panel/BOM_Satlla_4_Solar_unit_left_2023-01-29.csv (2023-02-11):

ID | Name | Designator | Footprint | Quantity | Manufacturer Part | Manufacturer | Supplier | Supplier Part | Price
1 | 1N5817W | D1 | SOD-123_L2.8-W1.8-LS3.7-RD | 1 | 1N5817W | TWGMC | LCSC | C727113 | 0.004
2 | Solar 1+ | J1 | CONNECTOR | 1 | RF130-1013BBS0741 |  | SeeedStudio | 320030026
3 | Solar 1- | J2 | CONNECTOR | 1 | RF130-1013BBS0741 |  | SeeedStudio | 320030026
4 | Solar 2+ | J3 | CONNECTOR | 1 | RF130-1013BBS0741 |  | SeeedStudio | 320030026
5 | Solar 2- | J4 | CONNECTOR | 1 | RF130-1013BBS0741 |  | SeeedStudio | 320030026
6 | Solar 3+ | J5 | CONNECTOR | 1 | RF130-1013BBS0741 |  | SeeedStudio | 320030026
7 | Solar 3- | J6 | CONNECTOR | 1 | RF130-1013BBS0741 |  | SeeedStudio | 320030026
8 | JST-ZH-2-PIN_HEADER TH | U1,U2 | JST-ZH-2 1.5MM TH | 2

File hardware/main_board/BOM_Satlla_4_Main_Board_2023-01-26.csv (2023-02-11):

ID | Name | Designator | Footprint | Quantity | Manufacturer Part | Manufacturer | Supplier | Supplier Part | Price | Pins | JLCPCB Part Class | JLCPCB SMD | LCSC Assembly | Contributor | Package Display | Resistance (Ohms) | SMT Type | description | image | link
1 | 10uF | C1,C2 | C0603 | 2 | GRM188R61C106MA73D | MuRata | LCSC | C86277 | 0.007 | 2 |  |  |  | LCSC
2 | 10pF | C3,C4 | C0603 | 2 | 0603CG100J101NT | FH | LCSC | C56033 | 0.001 | 2 | Extended Part
3 | 22uF | C5,C6,C7 | C0805 | 3 | GRM219R61C226ME15L | Murata Electronics | LCSC | C162295 | 0.027 | 2 |  |  |  | LCSC
4 | 100nF | C8 | C0603 | 1 | 0603F104M500NT | FH | LCSC | C42998 |  | 2 | Extended Part
5 | SS34_C8678 | D1 | DO-214AC_L4.3-W2.7-LS5.3-RD | 1 | SS34 | MDD | LCSC | C8678 | 0.005 | 2 | Basic Part
6 | 1206L075/13.2WR | F2 | F1206 | 1 | 1206L075/13.2WR | Littelfuse | LCSC | C207036 | 0.034 | 2 |  |  |  | LCSC
7 | 5.6uH | L1 | IND-SMD_L5.4-W5.2 | 1 | YSPI0530-5R6M | YJYCOIN | LCSC | C497860 | 0.034 | 2 |  |  |  | LCSC
8 | AO3401A | Q1,Q3,Q9,Q10,Q11 | SOT-23_L2.9-W1.3-P1.90-LS2.4-BR | 5 | AO3401A | AOS | LCSC | C15127 | 0.014 | 3 | Basic Part |  |  |  | No
9 | AO3400A | Q2,Q4,Q5,Q6,Q7,Q8,Q12,Q13 | SOT-23-3_L2.9-W1.6-P1.90-LS2.8-BR | 8 | AO3400A | AOS | LCSC | C20917 | 0.015 | 3 |  | Yes | Yes |  |  |  | Basic |  | //image.lceda.cn/szlcsc/C20917.jpg
10 | AO3401A_C347476 | Q14 | SOT-23_L2.9-W1.3-P1.90-LS2.4-BR | 1 | AO3401A | Youtai Semiconductor Co., Ltd. | LCSC | C347476 | 0.005 | 3 | Extended Part |  |  | LCSC
11 | 100K | R1,R2 | R0603 | 2 | RC0603JR-07100KL | YAGEO | LCSC | C100048 |  | 2 | Extended Part |  |  | LCSC
12 | 4.7K | R3,R6 | R0603 | 2 | RMC06034.7K1%N | Tyohm | LCSC | C269713 |  | 2 | Extended Part |  |  | LCSC
13 | 10K | R4,R5,R7,R8,R9,R10,R11,R12,R13,R19,R20,R22,R23,R24 | R0603 | 14 | 0603WAF1002T5E | UniOhm | LCSC | C25804 |  | 2 |  | Yes | Yes |  |  |  | Basic
14 | 1M | R14 | R0603 | 1 | ERJ3GEYJ105V | PANASONIC | LCSC | C278634 | 0.001 | 2 |  |  |  | LCSC
15 | 0r | R15,R17 | R0603 | 2 |  |  |  |  |  | 2 |  |  |  | LCEDA_Lib
16 | 0Ω | R16 | R0603 | 1 | 0603WAF0000T5E | UniOhm | LCSC | C21189 |  | 2 | Basic Part |  |  |  |  | 0
17 | KH-IPEX-K501-29 | RF1 | ANT-SMD_KH-IPEX-K501-29 | 1 | KH-IPEX-K501-29 | Shenzhen Kinghelm Elec | LCSC | C411563 | 0.011 | 4 | Extended Part |  |  | LCSC
18 | JST-ZH-4-PIN_HEADER | U1,U2,U3,U10,U12,U13 | JST-ZH-4 1.5MM | 6 |  |  |  |  |  | 4
19 | MAX6369KA+T | U4 | SOT-23-8_L3.0-W1.7-P0.65-LS2.8-TL | 1 | MAX6369KA+T | MAXIM | LCSC | C128613 | 0.163 | 8 | Extended Part
20 | LORA-RA-02-433MHZ | U5 | LORA-RA2-SMD | 1 |  |  |  |  |  | 16 |  |  |  | איגור אוצ\'נסקי |  |  |  | 433 MHz Lora Ra-02 Radio Transceiver Module based on SX1276 chip.
21 | JST-ZH-2-PIN_HEADER TH | U6,U7,U14,U15,U16,U18,U21 | JST-ZH-2 1.5MM TH | 7 |  |  |  |  |  | 2 |  |  |  | Herve Goncalves
22 | NavSpark-mini | U8 | NAVSPARK-MINI | 1 |  |  |  |  |  | 12 |  |  |  | tpallay | No
23 | Adafruit LIS3MDL | U9 | 9 DOF IMU_SATLLA_3 | 1 |  | Adafruit | Mouser | 485-4479 |  | 10 |  |  |  | ABDC |  |  |  |  |  | https://learn.adafruit.com/lis3mdl-triple-axis-magnetometer
24 | LoRa1280F27 | U17 | LORA1280F27 | 1 |  |  |  |  |  | 18 |  |  |  | jyesmith |  |  |  |  |  | https://www.nicerf.com/product_146_301.html
25 | TEENSY_41_ASMITH | U19 | TEENSY-4.1-ALL-PINS-ASMITH | 1 |  |  |  |  |  | 58 |  |  |  | diaphone
26 | MY-1220-03 SMT BATTERY CONNECTORS COPY | U20 | MY-1220-03 SMT COPY | 1 |  |  |  |  |  | 3 |  |  |  | igselyanko | No |  |  |  |  | https://datasheet.lcsc.com/lcsc/2012181809_MYOUNG-MY-1220-03_C964818.pdf
27 | TPS63061DSCT | U22 | WSON-10_L3.0-W3.0-P0.50-BL-EP | 1 | TPS63061DSCT | TI | LCSC | C134127 | 0.989 | 19 |  |  | Yes |  |  |  | Extend

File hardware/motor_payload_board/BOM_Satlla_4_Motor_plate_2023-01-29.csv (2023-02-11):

ID | Name | Designator | Footprint | Quantity | Manufacturer Part | Manufacturer | Supplier | Supplier Part | Price
1 | XT30PW-F | H1 | XT30PW-F | 1 | XT30PW | Amass | banggood | 1075324
2 | AO3400A | Q11 | SOT-23-3_L2.9-W1.6-P1.90-LS2.8-BR | 1 | AO3400A | AOS | LCSC | C20917 | 0.015
3 | AO3401A | Q12 | SOT-23_L2.9-W1.3-P1.90-LS2.4-BR | 1 | AO3401A | AOS | LCSC | C15127 | 0.014
4 | 10K | R14,R16 | R0603 | 2 | 0603WAF1002T5E | UniOhm | LCSC | C25804
5 | JST-ZH-4-PIN_HEADER | U1 | JST-ZH-4 1.5MM | 1

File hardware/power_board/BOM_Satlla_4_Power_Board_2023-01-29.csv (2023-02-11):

ID | Name | Designator | Footprint | Quantity | Manufacturer Part | Manufacturer | Supplier | Supplier Part | Price
1 | BATTERY_18350 | BATTERY1,BATTERY2 | 18350 WITH PROTECTION | 2 | file:///Users/leo/Downloads/54.PDF | https://www.keyelco.com/product.cfm/For-17-19mm-Dia-Lithium-Ion-Batteries/54/product_id/826
2 | 10uF | C1 | C1206 | 1 | CL31A106KBHNNNE | SAMSUNG | LCSC | C13585 | 0.005
3 | 100nF | C2 | C1206 | 1 | CL31B104KBCNNNC | SAMSUNG | LCSC | C24497 | 0.002
4 | XT30 | CN1 | CONN-TH_XT30UPB-F | 1 | XT30UPB-F |  | LCSC | C108769 | 0.053
5 | 1N5817W | D1 | SOD-123_L2.8-W1.8-LS3.7-RD | 1 | 1N5817W | TWGMC | LCSC | C727113 | 0.004
6 | Solar 1+ | J1 | CONNECTOR | 1 | RF130-1013BBS0741 |  | SeeedStudio | 320030026
7 | Solar 1- | J2 | CONNECTOR | 1 | RF130-1013BBS0741 |  | SeeedStudio | 320030026
8 | Solar 2+ | J3 | CONNECTOR | 1 | RF130-1013BBS0741 |  | SeeedStudio | 320030026
9 | Solar 2- | J4 | CONNECTOR | 1 | RF130-1013BBS0741 |  | SeeedStudio | 320030026
10 | Solar 3+ | J5 | CONNECTOR | 1 | RF130-1013BBS0741 |  | SeeedStudio | 320030026
11 | Solar 3- | J6 | CONNECTOR | 1 | RF130-1013BBS0741 |  | SeeedStudio | 320030026
12 | 17-21SURC/S530-A3/TR8 | LED1,LED2 | LED0805-R-RD | 2 | 17-21SURC/S530-A3/TR8 | EVERLIGHT | LCSC | C72037 | 0.003
13 | 1K | R1,R2 | R1206 | 2 | RK73B2BTTD102J | KOA Speer Elec | LCSC | C192527
14 | 1.2K | R4 | R1206 | 1 | RMC12061.2K1%N | Tyohm | LCSC | C269579 | 0.001
15 | MICROSWITCH KW12-3 | S1,S2 | BI0002405 | 2 | AVT34243 | Panasonic | RS-Online | 173-8372
16 | JST-ZH-4-PIN_HEADER | U1,U4 | JST-ZH-4 1.5MM | 2
17 | JST-ZH-2-PIN_HEADER TH | U2 | JST-ZH-2 1.5MM TH | 1
18 | TP4056_C382139 | U3 | ESOP-8_L4.9-W3.9-P1.27-LS6.0-BL-EP | 1 | TP4056 | TPOWER | LCSC | C382139 | 0.02
19 | SparkFun_Battery_Babysittero | U12 | SPARKFUN_BATTERY_BABYSITTE_KCG | 1 | SparkFun
20 | micro 5PFour-legged board7.2There is a column card point0.4m | USB1,USB2 | MICRO-USB-SMD_5P-P0.65-H-F-C40943 | 2 | micro 5PFour-legged board7.2There is a column card point0.4m | ValuePro | LCSC | C40943 | 0.016

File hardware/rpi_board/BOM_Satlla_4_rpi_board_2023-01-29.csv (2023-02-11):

ID | Name | Designator | Footprint | Quantity | Manufacturer Part | Manufacturer | Supplier | Supplier Part | Price
1 | 1N5817W | D1 | SOD-123_L2.8-W1.8-LS3.7-RD | 1 | 1N5817W | TWGMC | LCSC | C727113 | 0.004
2 | Solar 1+ | J1 | CONNECTOR | 1 | RF130-1013BBS0741 |  | SeeedStudio | 320030026
3 | Solar 1- | J2 | CONNECTOR | 1 | RF130-1013BBS0741 |  | SeeedStudio | 320030026
4 | Solar 2+ | J3 | CONNECTOR | 1 | RF130-1013BBS0741 |  | SeeedStudio | 320030026
5 | Solar 2- | J4 | CONNECTOR | 1 | RF130-1013BBS0741 |  | SeeedStudio | 320030026
6 | Solar 3+ | J5 | CONNECTOR | 1 | RF130-1013BBS0741 |  | SeeedStudio | 320030026
7 | Solar 3- | J6 | CONNECTOR | 1 | RF130-1013BBS0741 |  | SeeedStudio | 320030026
8 | RASPBERRY PI ZERO HEADER | RPI1 | RASPBERRY_PI_ZERO HEADER_NEW | 1 | Raspberry Pi Zero WH | Raspberry Pi Foundation | Pollin | 810885
9 | JST-ZH-4-PIN_HEADER | U1,U3,U7 | JST-ZH-4 1.5MM | 3
10 | JST-ZH-2-PIN_HEADER TH | U2,U4,U5,U6,U8 | JST-ZH-2 1.5MM TH | 5

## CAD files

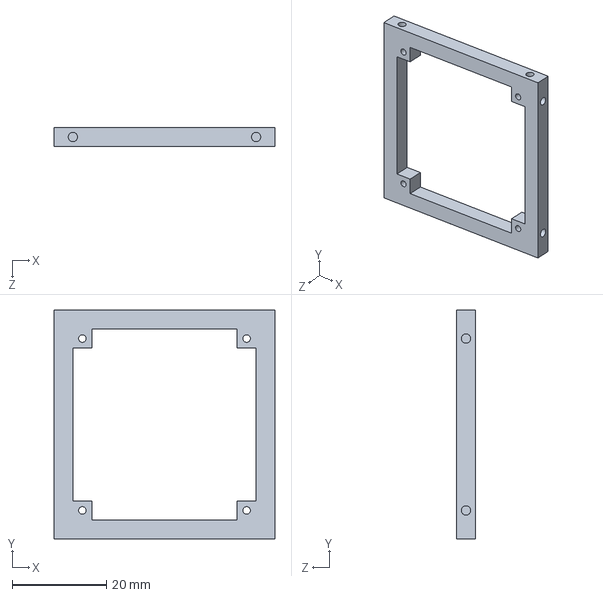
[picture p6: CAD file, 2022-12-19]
stl/left-right-holders.SLDPRT
46.8 x 48.4 x 4.00 mm

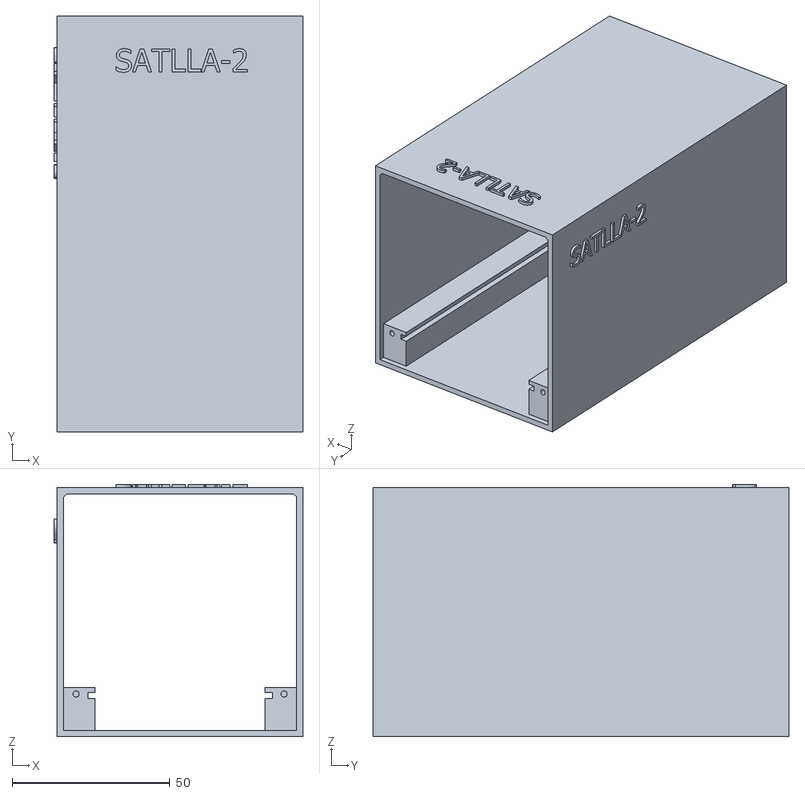
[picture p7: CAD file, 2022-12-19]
stl/pod_box.stl
79.0 x 132.0 x 80.0

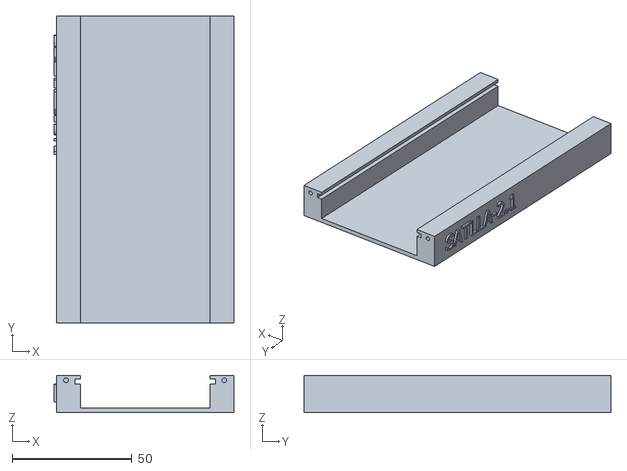
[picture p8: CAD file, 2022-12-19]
stl/pod_rails.stl
75.0 x 128.0 x 15.5

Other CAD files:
stl/left_panel.stl

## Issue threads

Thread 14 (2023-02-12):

Repository documentation and structure

federeghe, 2023-02-12:
This issue is part of the JOSS review: https://github.com/openjournals/joss-reviews/issues/5147

I think that the README should be improved, especially if the repository is meant for students. Opening the repository without the paper provides no information of what the repository contains (hardware? software? an operating systems? a set of on-board tasks? etc.).

For instance, the README is missing:
- [x] Detailed statements on what the repository contains
- [x] A clear list of features
- [x] The list of supported boards/processors (From the README seems Arduino, but it is actually a Raspberry the OBC)
- [x] What is Master/OBC/Ground

I would also revise the directory structure of the repository. I don't expect to find a `docs` directory but the documentation is elsewhere (Wiki + *.md files in the root). The `docs` contains, instead, the structural design and hardware files. My suggestion is to re-organize the directory structure, something like: `hardware/`, `software/`, `stl/`, `paper/`, etc. These are only the first words popped up in my mind, feel free to choose any names you like but I suggest a more structured directory tree.

ronyronen, 2023-02-13:
@federeghe thanks for your feedback. I've updated the repository and published a new version: 4.0.8.

Closed 2023-02-13.

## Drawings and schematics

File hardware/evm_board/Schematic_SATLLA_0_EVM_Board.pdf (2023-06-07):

## Teensy3.2

## Adafruit 4479 IMU

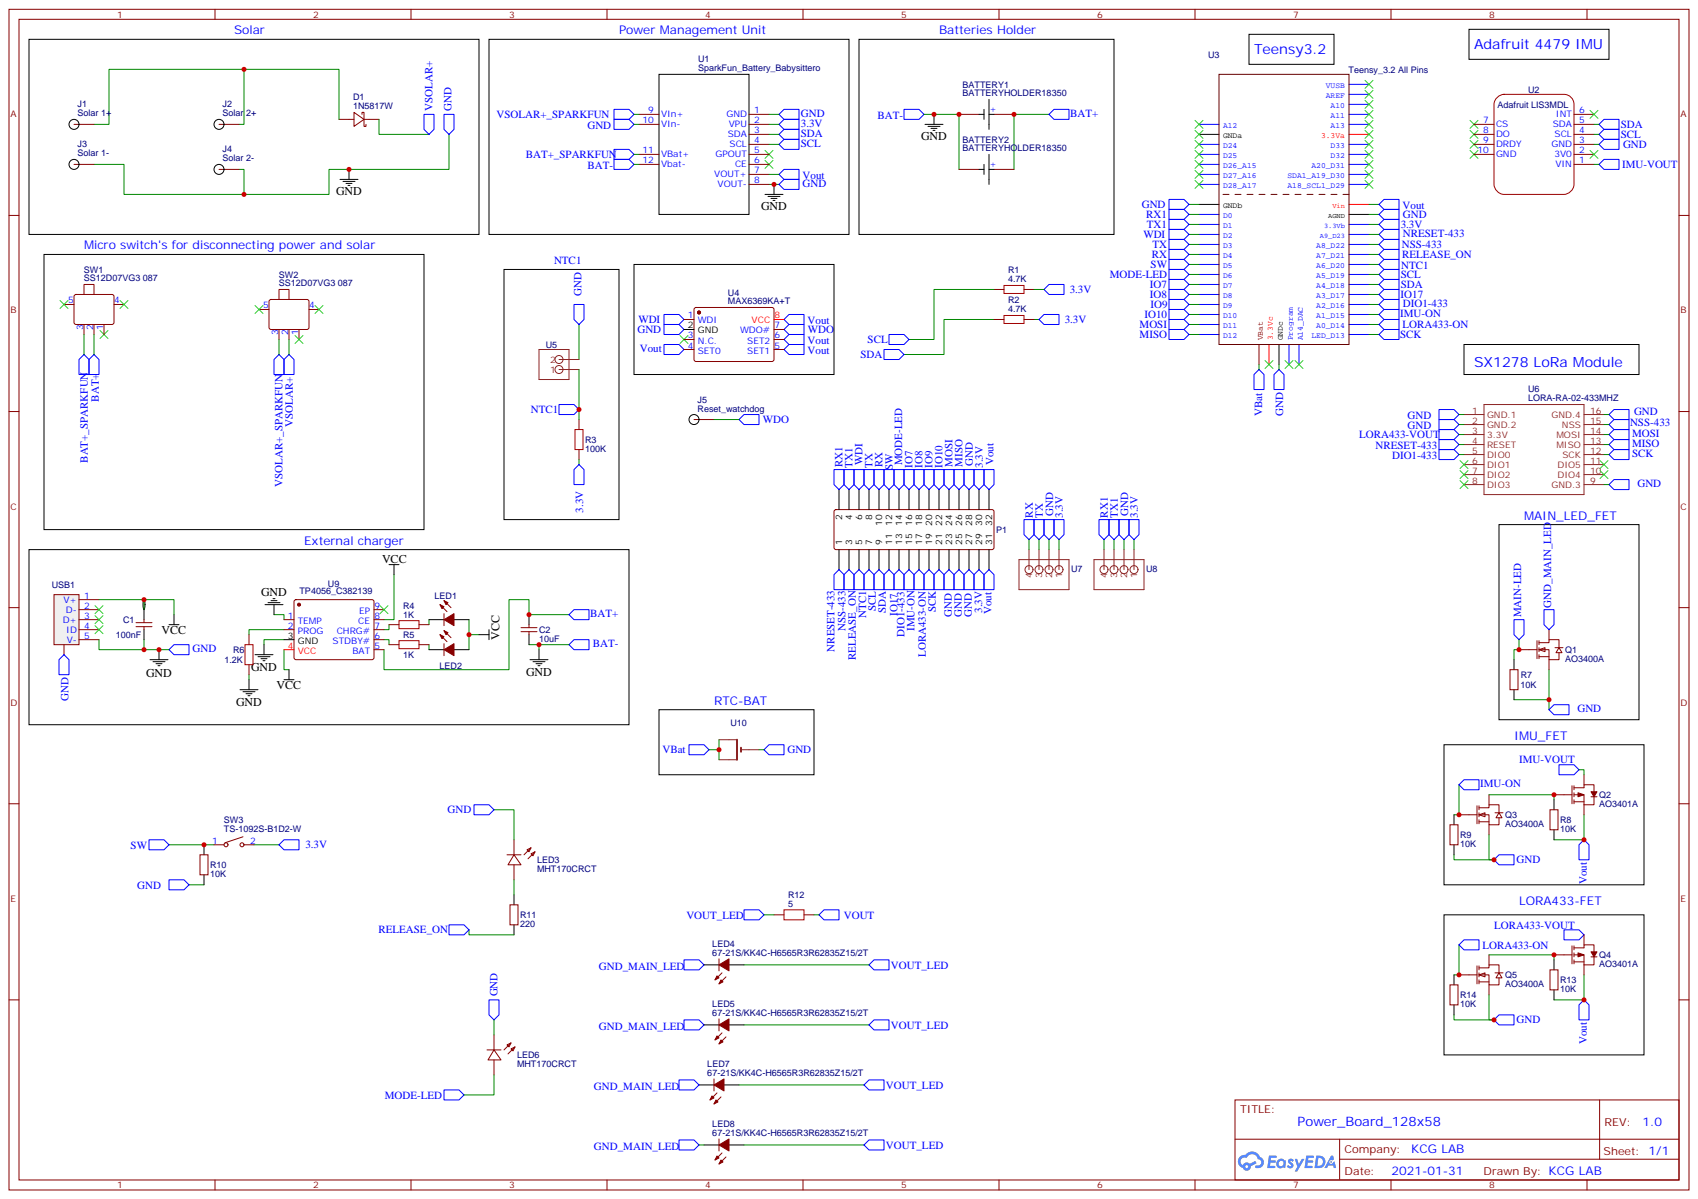
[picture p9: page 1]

Micro switch's for disconnecting power and solar

Drawn By: KCG LAB

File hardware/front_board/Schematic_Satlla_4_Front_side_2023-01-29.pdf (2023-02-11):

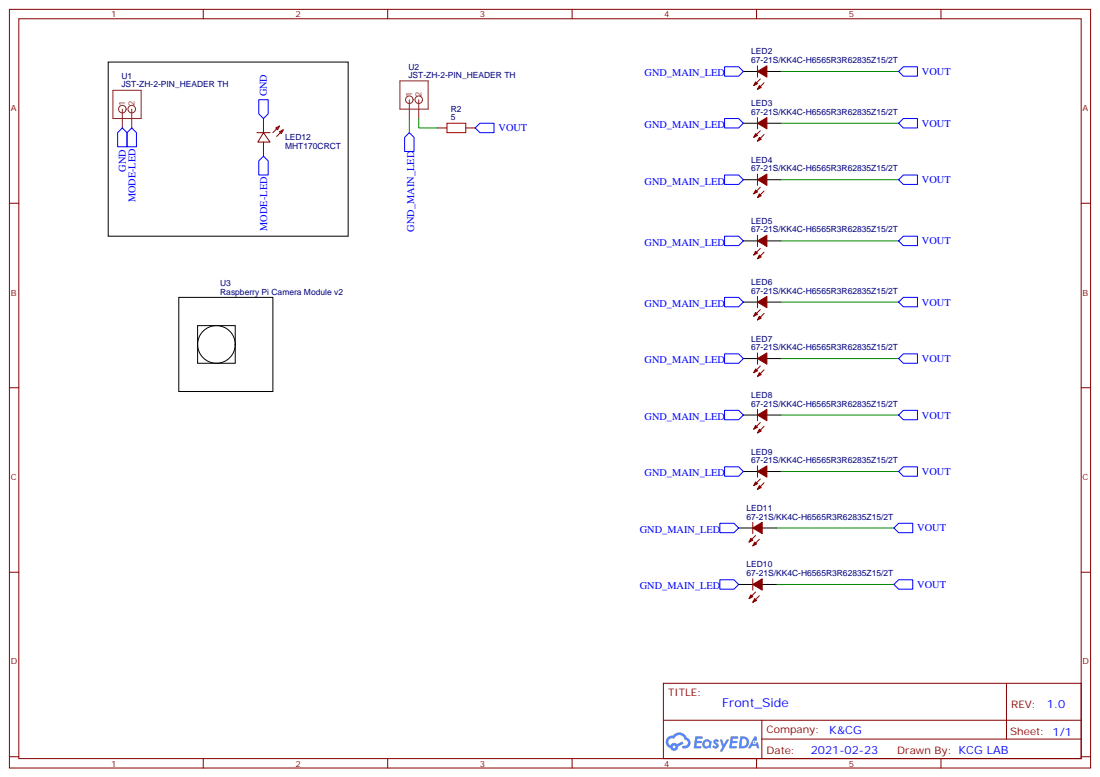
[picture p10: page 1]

Raspberry Pi Camera Module v2

Drawn By: KCG LAB

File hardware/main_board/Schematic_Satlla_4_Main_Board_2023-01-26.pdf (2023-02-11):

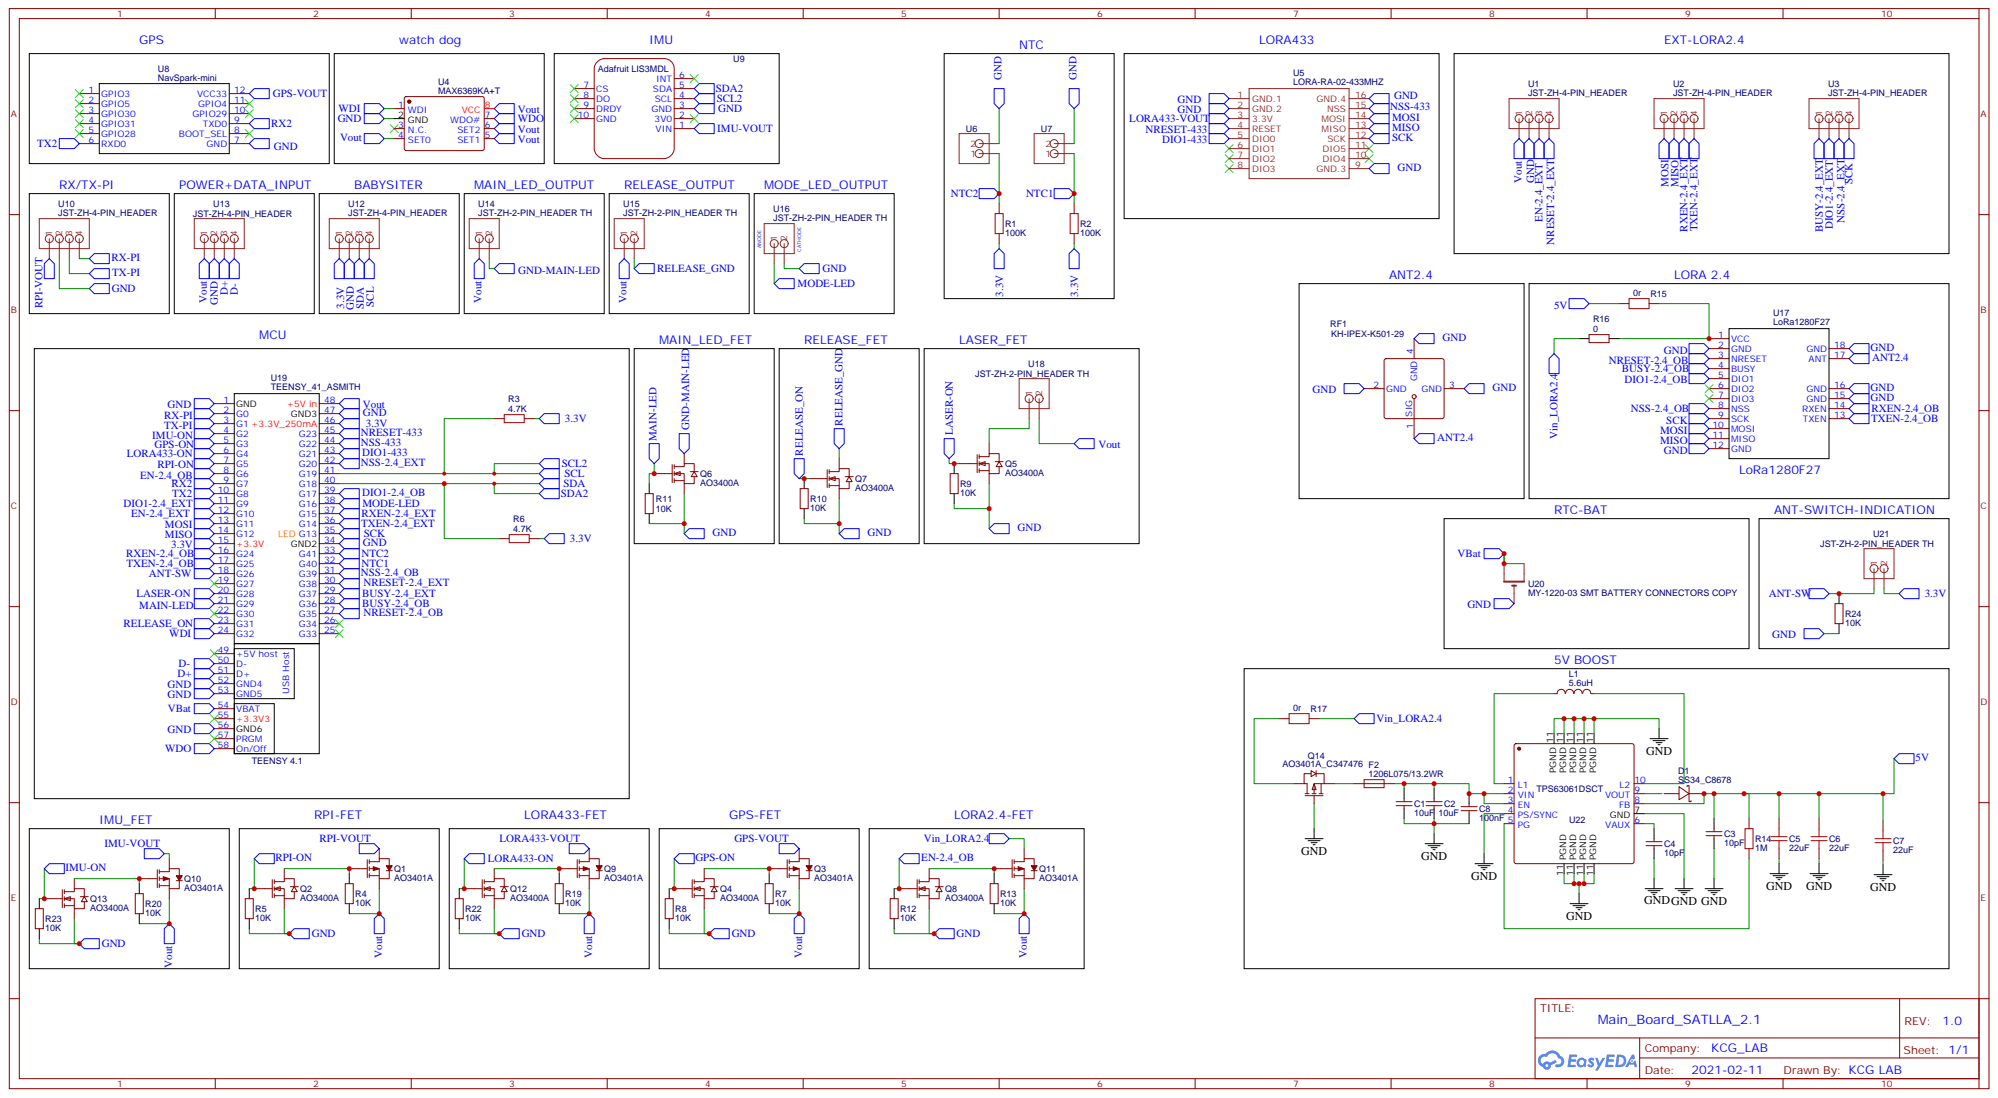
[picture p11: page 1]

MY-1220-03 SMT BATTERY CONNECTORS COPY

Drawn By: KCG LAB

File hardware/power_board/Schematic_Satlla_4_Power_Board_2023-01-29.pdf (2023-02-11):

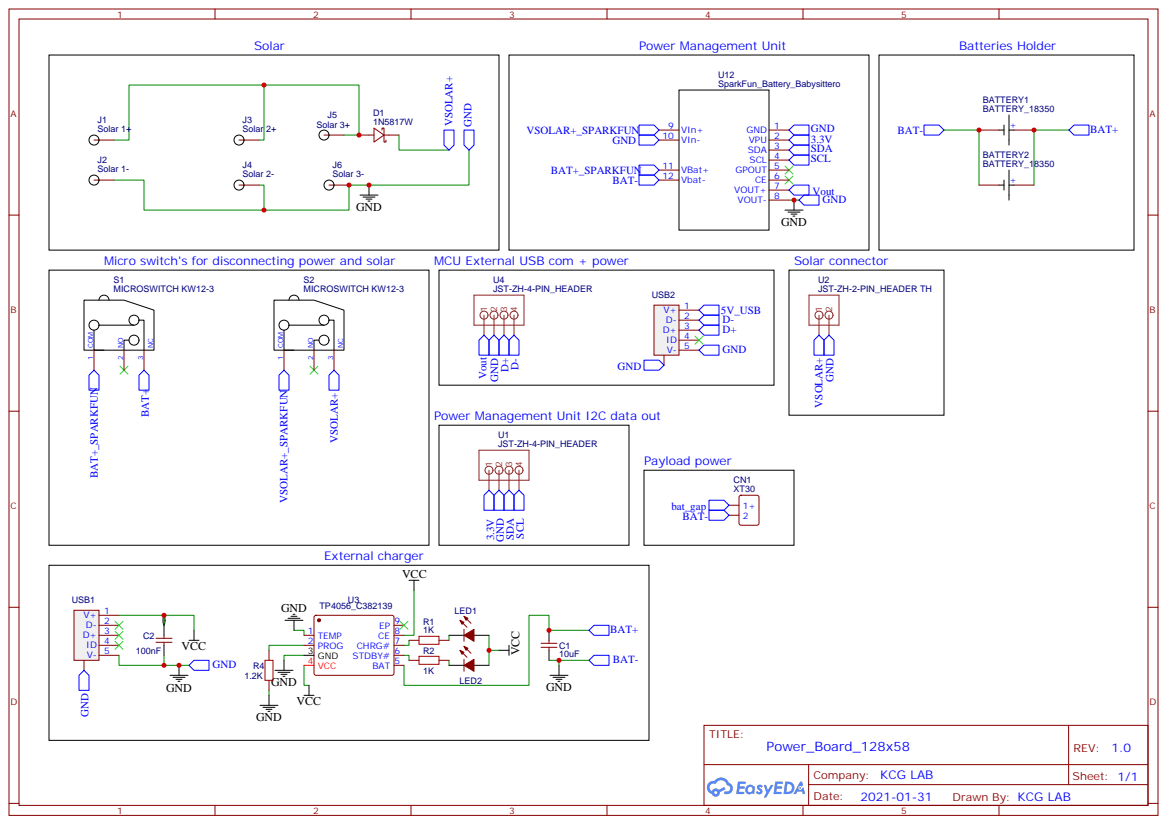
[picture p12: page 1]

Power Management Unit I2C data out

Drawn By: KCG LAB

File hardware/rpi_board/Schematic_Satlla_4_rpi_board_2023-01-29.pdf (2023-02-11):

A | A

1

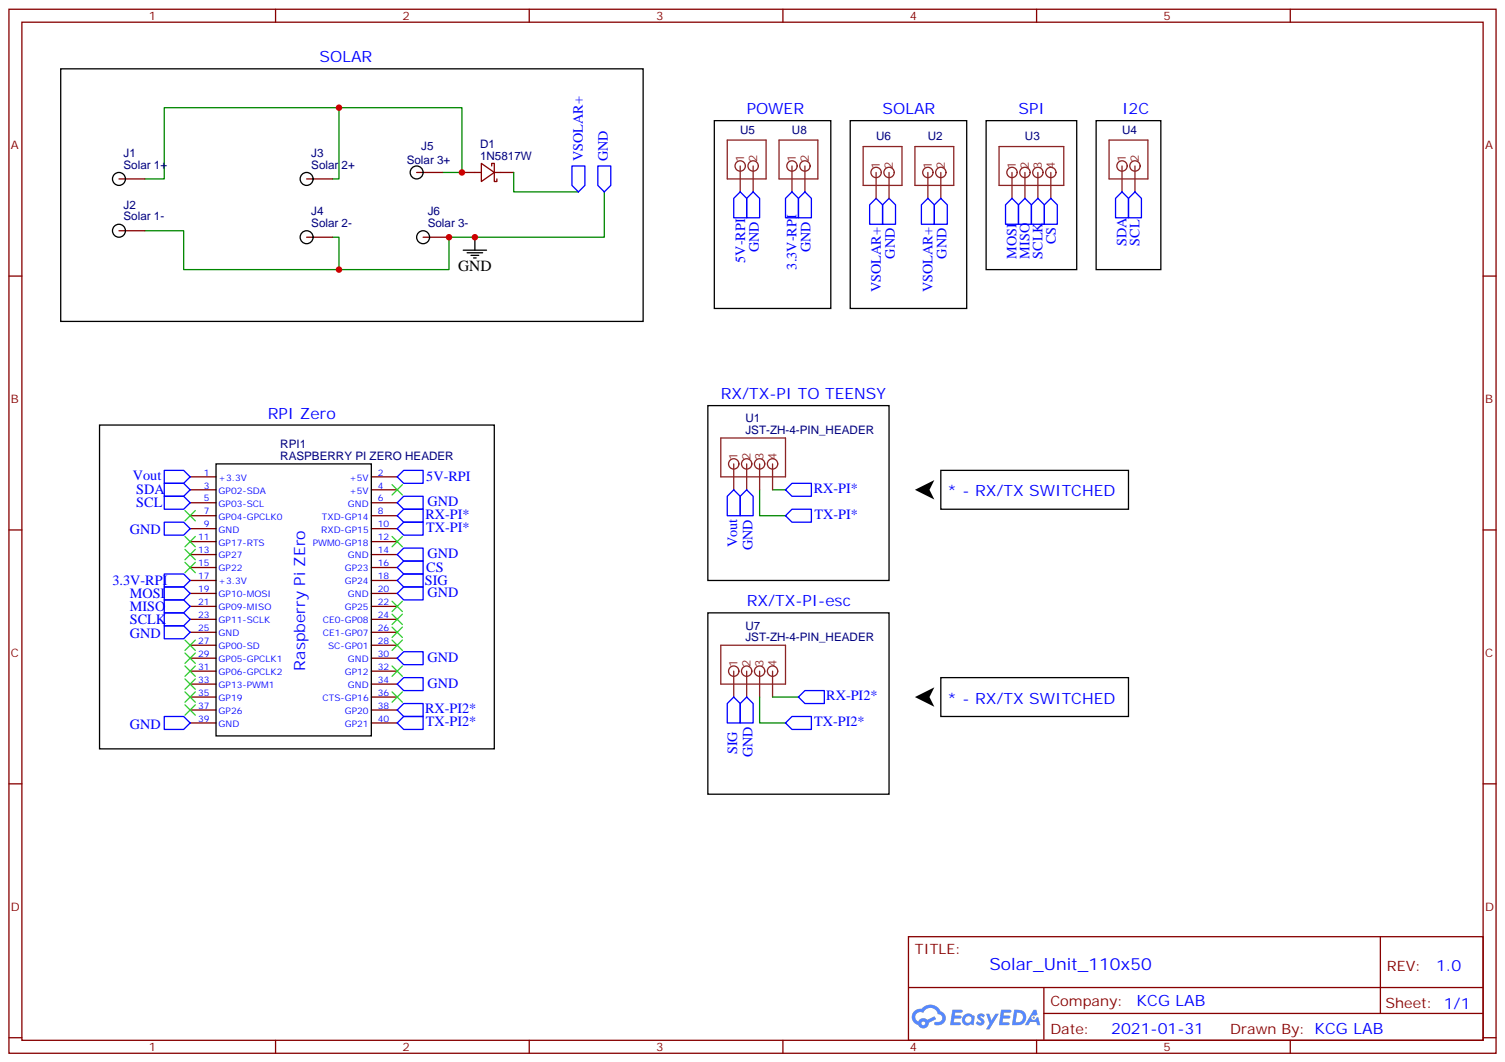
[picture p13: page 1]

RX/TX-PI TO TEENSY
JST-ZH-4-PIN_HEADER

RPI1
RASPBERRY PI ZERO HEADER

RX/TX-PI-esc

Drawn By: KCG LAB

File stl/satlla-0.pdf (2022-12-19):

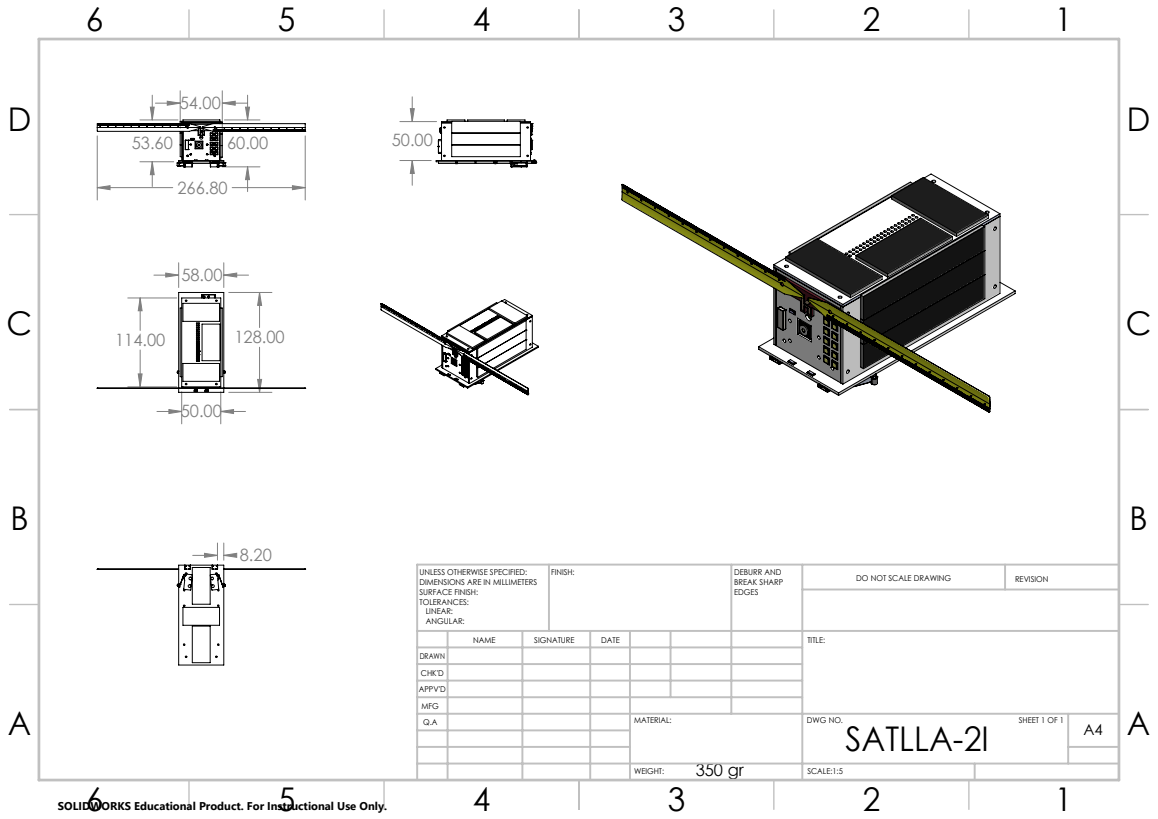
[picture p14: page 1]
FINISH:; DEBURR AND; BREAK SHARP; DO NOT SCALE DRAWING; REVISION

UNLESS OTHERWISE SPECIFIED:
DIMENSIONS ARE IN MILLIMETERS
SURFACE FINISH:
TOLERANCES:
LINEAR:
ANGULAR:

NAME | SIGNATURE | DATE | | | | TITLE:

DRAWN
CHK'D
APPV'D
MFG
Q.A | | | | MATERIAL: | DWG NO. SATLLA-2I SHEET 1 OF 1 | A4

SOLIDWORKS Educational Product. For Instructional Use Only.

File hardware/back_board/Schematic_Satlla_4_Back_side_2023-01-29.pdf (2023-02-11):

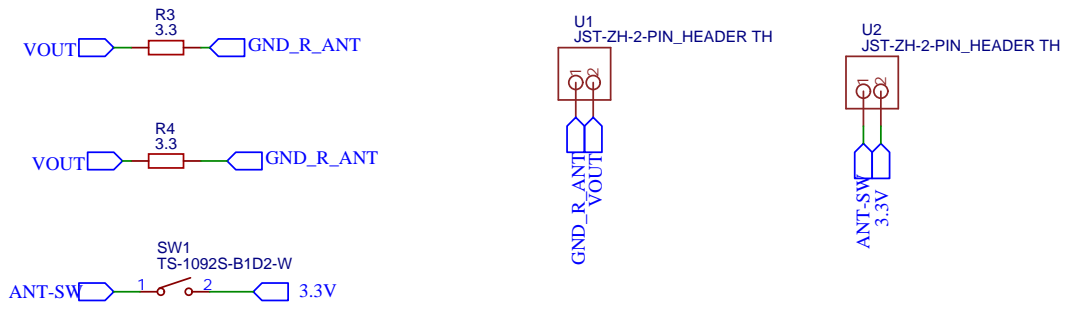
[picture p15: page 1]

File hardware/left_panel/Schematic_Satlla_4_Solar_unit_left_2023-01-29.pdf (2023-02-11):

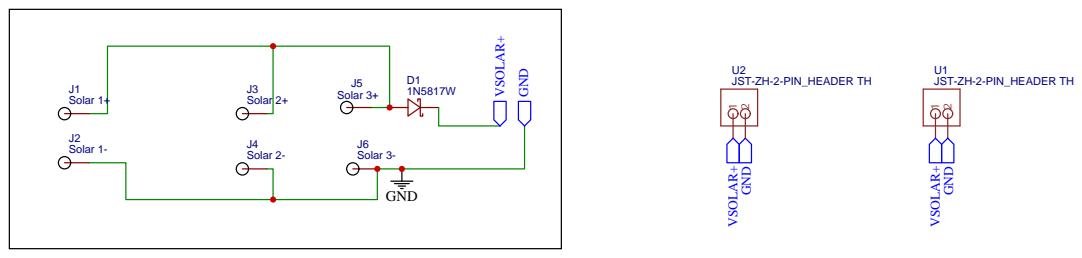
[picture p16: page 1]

Drawn By: KCG LAB

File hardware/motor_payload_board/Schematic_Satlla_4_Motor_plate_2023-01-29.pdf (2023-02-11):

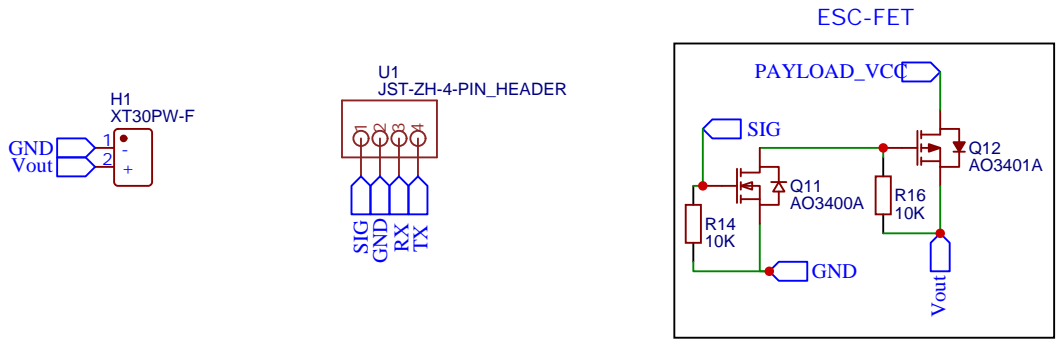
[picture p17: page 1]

Drawn By: KCG LAB

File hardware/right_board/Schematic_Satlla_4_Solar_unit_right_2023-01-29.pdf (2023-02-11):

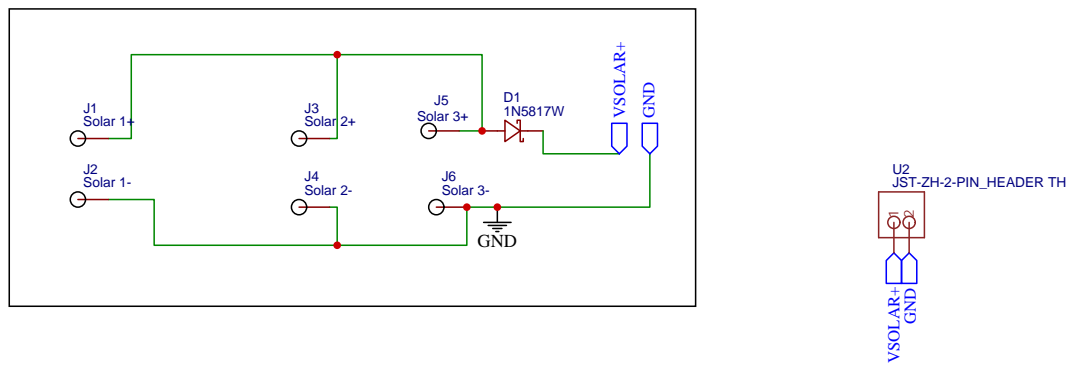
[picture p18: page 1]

Drawn By: KCG LAB

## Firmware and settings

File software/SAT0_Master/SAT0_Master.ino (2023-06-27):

/**
    @file SAT0_Master.ino
    @brief Master file for SATLLA0.
    This contains the main setup and main loop of the SAT.
    Board: Teensy 3.6
    Copyright (C) 2023 @author Rony Ronen

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
    You should have received a copy of the GNU General Public License
    along with this program.  If not, see <https://www.gnu.org/licenses/>.
*/

#define programversion "SATLLA0"
#define Serial_Monitor_Baud 115200

#include "settings.h"

/* ============ */
/* Setup        */
/* ============ */

void setup()
{
    Serial.begin(Serial_Monitor_Baud);
    delay(SEC_1);

    PRINTLN("************* START SETUP *************");

    PRINTLN();
    PRINT(__TIME__);
    PRINT(F(" "));
    PRINTLN(__DATE__);
    PRINTLN(programversion);
    PRINTLN(SAT_NAME);
    PRINT("F_CPU: ");
    PRINTLN(ltoa(F_CPU, buffer_g, 10));
    if (F_CPU > 24000000)
    {
        PRINTLN("Warning: CPU speed should be reduced to keep power consumption low!");
    }
    PRINTLN();

#if RTC_ENABLE
    // set the Time library to use Teensy 3.0's RTC to keep time
    setSyncProvider(getTeensy3Time);

    if (timeStatus() == timeNotSet)
    {
        // setTime(00,00,00,01,01,2023);
        rtc_setup();
        Teensy3Clock.set(now());
    }
    digitalClockDisplay();
    delay(TENTH_SEC);
#endif

    // SPI
    PRINTLN(F("SCK PIN: 13"));
//     SPI.setSCK(13); // For teensy 3.6/4.1 - Default
    SPI.begin();
    delay(TENTH_SEC);

    Wire.begin();
    delay(TENTH_SEC);

    sat_state = sat_high_power;

    // FATs
    setup_fat_pin_out();

    // Watchdog Setup
#if WD_ENABLE
    wd_setup();
    delay(TENTH_SEC);
#endif

    // SD Card Setup
#if SD_ENABLE
    SD_Card_setup();
    delay(TENTH_SEC);
#endif

    // Large FS if Teensy 4.1
#if TNSYFS_ENABLE
    tnsyfs_setup();
    delay(TENTH_SEC);
#endif

    // Mode LED
#if MODELED_ENABLE
    modeled_setup();
#endif

    // Blink LED
#if MAINLED_ENABLE
    LED_setup();
#endif

    // Blink Laser
#if LASER_ENABLE
    laser_setup();
#endif

    // Global Settings Setup
#if EEPROM_ENABLE
    get_global_settings();
    // reset_global_setting();
    delay(TENTH_SEC);
#endif

    // IMU
#if IMU_ENABLE
    // IMU - LSM6DS33
    imu_turn_on(); // calling sensor_imu_setup()
    // imu_read();
#if IMU_LSM6DS33_ENABLE
    // sensor_imu_setup(); // calling sensor_imu_setup()
    imu_read();
#endif
    delay(TENTH_SEC);
#endif

    // GPS
#if GPS_ENABLE
    // turn on
    gps_turn_on();
    gps_setup();
    delay(TENTH_SEC);
#endif

    // NTC's
#if NTC_ENABLE
    sensor_ntc_setup();
#endif

    // SF BBSTR
#if BBSTR_BQ27441_ENABLE
    setup_BQ27441();
    delay(TENTH_SEC);
    battery_read();
    check_battery_status();
#endif

    // RPI 0
#if RPI_ENABLE
    rpi_serial_setup();
    delay(TENTH_SEC);
#endif

    // LoRa 433 Setup
#if RF_433_ENABLE
    lora_433_turn_on();
    delay(TENTH_SEC);
    modem_fsk_433_setup(); // Need to set FSK as well

    lora_433_setup();
#endif

    // LoRa SX1280
#if RF_24_ENABLE
    lora_24_turn_on();
    delay(TENTH_SEC);

    lora_24_setup();
    lora_433_setup(); // fix the issue of timeout -5
#endif

    // initial Boot include antenna deploy
    initial_boot();

    // set flags to false
    received_433_flag = false;

    // increment restart index
#if SD_ENABLE
    if (sdcard_is_on)
    {
        inc_reset_index();
    }
#endif

#if TNSYFS_ENABLE
    if (!sdcard_is_on || save_to_flash)
    {
        if (flash_is_on)
        {
            fs_inc_reset_index();
        }
    }
#endif
    delay(TENTH_SEC);

    PRINTLN("**************************  END SETUP ************************** ");
}

/* ============ */
/* Loop         */
/* ============ */

void loop()
{
    PRINTLN("************************** START LOOP **************************");
    PRINT("Func: loop()");
    loop_start_millis = millis();
    PRINT(", Secs:\t");
    PRINTLN(loop_start_millis / SEC_1);

#if RTC_ENABLE
#ifdef DEBUG
    digitalClockDisplay();
#endif
#endif
    // WD pulse
#if WD_ENABLE
    wd_heartbeat();
#endif

    // battery read
#if BBSTR_BQ27441_ENABLE
    battery_read();
    // set sat power: panic, med, high
    check_battery_status();
#endif

    // check health
    set_sat_health();

    // if battery is high or 1 hour pass from last beacon, enable sending beacon
    if (sat_state > sat_panic_power || loop_start_millis - last_sent_beacon_time > HOUR_1) // > 3500
    {
        // send beacon procedure:
        // send 433. wait 1 sec. send 2.4. wait for Rx 20 sec.
        // sleep
        if (loop_start_millis - last_sent_beacon_time > send_beacon_threshold)
        {
            // set long or short beacons
            b_type = (beacon_type_e)switch_beacon_type();
            // prepare the beacon
            handle_beacon(b_type, false); // (beacon, save to log flag).
#if RF_433_ENABLE
            // send via 433
            send_beacon(b_type, lora_433);
#endif
            last_sent_beacon_time = millis();

#if RF_24_ENABLE
            if (sat_state > sat_med_power) // > 3500
            {
                // smart delay between beacons
                smart_delay(delay_between_beacons); // 2 secs
                // send via 24
                send_beacon(b_type, lora_24);
            }
#endif
        }
    }

    // smart delay: keep Radio and GPS feed
    // listen for incoming messages
    smart_delay(ts_loop_runtime); // default 20 secs

    // general method to handle tasks.
    // if command arrive, it will be after the smart delay
    handle_tasks();

    // if mission started, then don't sleep during that period.
    if (!in_mission())
    {
#if RF_433_ENABLE
        // if GFSK is allowed, send a GFSK beacon.
        if (gfsk_beacon && sat_state > sat_panic_power) // > 3500
        {
            // switch to GFSK mode.
            set_modem(modem_fsk_433);
            // send beacon
            send_beacon(b_type, lora_433);
            // no wait for incoming GFSK so switch back to LoRa
            set_modem(modem_lora_433);
        }
#endif

#if MODELED_ENABLE
        stop_modeled_thread();
#endif

        unsigned long min_sleep_delay = min(sleep_delay_non_panic, millis() - last_sent_beacon_time);
        if (sat_state <= sat_panic_power)
        {
            min_sleep_delay = sleep_delay_panic;
        }
        // else, sleep for 15 secs.
        sleep_delay(min_sleep_delay); // milliseconds

#if MODELED_ENABLE
        start_modeled_thread();
#endif
    }

    PRINTLN("************************** END LOOP **************************");
}

/* ============ */
/* smart_delay  */
/* ============ */

static void smart_delay(const unsigned long ms)
{
    PRINTLN("************* START SMART_DELAY *************");
    PRINT("Func: smart_delay() For:\t");
    PRINTLN(ms / SEC_1);

    unsigned long start = millis();

    PRINT("Secs:\t");
    PRINTLN(start / SEC_1);

    // loop smart delay
    while (millis() - start < ms && start)
    {

#if GPS_ENABLE
        // feed gps
        if (gps_is_on)
        {
            feed_gps1();
        }
#endif

#if RF_433_ENABLE
        // message recevied, break and handle
        if (received_433_flag)
        {
            // break the loop
            break;
        }
#endif

#if RF_24_ENABLE
        // message recevied, break and handle
        if (received_24_flag)
        {
            // break the loop
            break;
        }
#endif

#ifdef DEBUG
        // serial recevied, break and handle
        if (Serial.available() || ant_button_state)
        {
            break;
        }
#endif

// watch dog
#if WD_ENABLE
        wd_heartbeat();
#endif
    }
    PRINTLN("************* END SMART_DELAY *************");

    // smart delay completed. if message arrived, process.
#if RF_433_ENABLE
    if (received_433_flag)
    {
        received_433_flag = false;
        delay(TENTH_SEC);
        handle_433_message();

#ifdef DEBUG
        // blink one long if got a message
        modeled_blink_period = MODELED_LONG;
        modeled_blink_count = 1;
#endif
    }
#endif

#if RF_24_ENABLE
    if (received_24_flag)
    {
        received_24_flag = false;
        delay(TENTH_SEC);
        on_receive_24();
        handle_24_message();
        setup_lora_24_rx();

#ifdef DEBUG
        // blink one long if got a message
        modeled_blink_period = MODELED_LONG;
        modeled_blink_count = 1;
#endif
    }
#endif

    // if stop tx requested, check if it pass threshold and reset flag
    if (stop_tx_flag > 0 && millis() - stop_tx_flag > STOP_TX_FLAG_THRESHOLD)
    {
        stop_tx_flag = 0;
    }

    // if restart requested wait 5 secs and restart
    if (restart_requested_flag)
    {
#ifdef DEBUG
        // blink one long if got a message
        modeled_blink_period = MODELED_LONG;
        modeled_blink_count = 3;
#endif
        restart_requested_flag = false;
        delay(SECS_3);
        CPU_RESTART;
    }

#ifdef DEBUG
    if (Serial.available() || ant_button_state)
    {
        serial_event();
    }
#endif
}

/* ============ */
/* sleep delay  */
/* ============ */

static void sleep_delay(const unsigned long ms)
{
    PRINTLN("************* START SLEEP_DELAY *************");
    PRINT("Func: sleep_delay() For:\t");
    PRINTLN(ms / SEC_1);

    unsigned long start = millis();

    PRINT("Secs:\t");
    PRINTLN(start / SEC_1);

#if IMU_ENABLE
    if (imu_is_on && !imu_is_sleep)
    {
        imu_sleep();
    }
#endif

#if RF_433_ENABLE
    if (lora_433_is_on && !lora_433_is_sleep)
    {
        lora_433_sleep();
    }
#endif

#if RF_24_ENABLE
    if (lora_24_is_on && !lora_24_is_sleep)
    {
        lora_24_sleep();
    }
#endif

#if GPS_ENABLE
    if (gps_is_on && !gps_is_sleep)
    {
        gps_sleep();
    }
#endif

// watchdog
#if WD_ENABLE
    wd_heartbeat();
#endif

    delay(ms);

    PRINTLN("************* RESUME SLEEP DELAY *************");

#if IMU_ENABLE
    if (imu_is_on && imu_is_sleep)
    {
        imu_resume();
    }
#endif

#if RF_433_ENABLE
    if (lora_433_is_on && lora_433_is_sleep)
    {
        lora_433_resume();
    }
#endif

#if RF_24_ENABLE
    if (lora_24_is_on && lora_24_is_sleep)
    {
        lora_24_resume();
    }
#endif

#if GPS_ENABLE
    if (gps_is_on && gps_is_sleep)
    {
        gps_resume();
    }
#endif

#ifdef DEBUG
    if (Serial.available())
    {
        serial_event();
    }
#endif

#if WD_ENABLE
    wd_heartbeat();
#endif

    PRINTLN("************* END SLEEP_DELAY *************");
}

/* ============== */
/* SAT In Mission */
/* ============== */

bool in_mission()
{
    PRINT("Func: in_mission():\t");
    bool ret_value = (mission_rpi_flag || mission_laser_blink_flag || mission_led_blink_flag);
    PRINTLN((ret_value) ? "true" : "false");
    return ret_value;
}

/* ============== */
/* SAT Health     */
/* ============== */

void set_sat_health()
{
    PRINTLN("Func: set_sat_health()");

    switch (sat_state)
    {
    case sat_panic_power:
    {
        PRINTLN("Sat Health: PANIC");
        // turn off all
#if GPS_ENABLE
        if (gps_is_on)
        {
            gps_turn_off();
        }
#endif

#if IMU_ENABLE
        if (imu_is_on)
        {
            imu_turn_off();
        }
#endif

#if RF_433_ENABLE
        if (lora_433_is_on)
        {
            lora_433_turn_off(); // TODO: preferred sleep
        }
        gfsk_beacon = false;
#endif

#if RF_24_ENABLE
        if (lora_24_is_on)
        {
            lora_24_turn_off();
        }
#endif

        modeled_blink_count = 3;
    }
    break;

    case sat_med_power:
    {
        PRINTLN("Sat Health: MEDIUM");
        // turn on LoRa, BNO and keep GPS off

#if GPS_ENABLE
        if (gps_is_on)
        {
            gps_turn_off();
        }
#endif

#if IMU_ENABLE
        if (!imu_is_on)
        {
            imu_turn_on();
        }
#endif

#if RF_433_ENABLE
        if (!lora_433_is_on)
        {
            lora_433_turn_on();
            delay(TENTH_SEC);
            lora_433_setup(); // after tuning on, need setup
        }
        gfsk_beacon = false;
#endif

#if RF_24_ENABLE
        if (lora_24_is_on)
        {
            lora_24_turn_off();
        }
#endif

        modeled_blink_count = 2;
    }
    break;

    case sat_high_power:
    {
        PRINTLN("Sat Health: HIGH");
        // turn on all
#if GPS_ENABLE
        if (!gps_is_on)
        {
            gps_turn_on();
        }
#endif

#if IMU_ENABLE
        if (!imu_is_on)
        {
            imu_turn_on();
        }
#endif

#if RF_433_ENABLE
        if (!lora_433_is_on)
        {
            lora_433_turn_on();
            delay(TEN_MS);    // let FATs times to go to HIGH
            lora_433_setup(); // after tuning on, need setup
        }
        gfsk_beacon = true;
#endif

#if RF_24_ENABLE
        if (!lora_24_is_on)
        {
            lora_24_turn_on();
            delay(TEN_MS); // let FATs times to go to HIGH
        }
        // resume checking the device. if problem occur will call setup.
        lora_24_resume();
#endif

        modeled_blink_count = 1;
    }
    break;

    default:
        break;
    }

#if GPS_ENABLE
    gps_health();
#endif
}

/* ================ */
/* Beacon Type */
/* ================ */
uint8_t switch_beacon_type()
{
    PRINTLN("Func: switch_beacon_type()");
    beacon_type_e b_type = beacon_type_long;
    // if mission started, send only long beacons.
    if (sat_state >= sat_med_power || in_mission())
    {
        b_type = beacon_type_long;
    }
    else
    {
        // if low power, then switch to short but keep 5 long each hr
        b_type = beacon_type_short;
        if (millis() - last_sent_long_beacon > HOUR_1)
        {
            b_type = beacon_type_long;
            sent_long_beacon_counter++;
            if (sent_long_beacon_counter > 5)
            {
                sent_long_beacon_counter = 0;
                last_sent_long_beacon = millis();
            }
        }
    }
    return b_type;
}

/* ============ */
/* Switch Modem */
/* ============ */

int16_t set_modem(modem_e modem)
{
    PRINTLN("Func: set_modem()");

    int16_t state = 0;

    if (current_modem == modem)
    {
        return state;
    }

    // initialize requested modem
    switch (modem)
    {
    case modem_lora_433:
#if RF_433_ENABLE
        setup_lora_433(&modem_lora_433_g);
#endif
        break;

    case modem_fsk_433:
    {
#if RF_433_ENABLE
        setup_fsk_433(&modem_fsk_433_g);
#endif
    }
    break;

    default:
        PRINT(F("Unknown modem: "));
        PRINTLN(modem);
        setup_lora_433(&modem_lora_433_g);
    }

    // radio.setWhitening(true, WHITENING_INITIAL);

    // handle possible error codes
    PRINT(F("Radio init "));
    PRINTLN(state);
    delay(TEN_MS);
    if (state != 0)
    {
        // radio chip failed, restart
    }

    // save current modem
    current_modem = modem;
    return (state);
}

/* ================ */
/* Auto Tasks IL  */
/* ================ */

int8_t handle_auto_tasks()
{
    PRINTLN("Func: handle_auto_tasks()");
    int8_t mission = 0x00;

    // Auto: Once a day
    memset(command_data_g.packet, 0x00, COMMAND_PACKET_LENGTH);

    unsigned long auto_task = millis() - last_auto_task;

    if (auto_task > DAY_1 && auto_task <= DAYS_2)
    {
        PRINTLN("Func: handle_auto_tasks()::rpi_cmd_take_photo");
        memcpy(command_data_g.packet, rpi_cmd_take_photo, 5); // 0x5500010004
        mission = 0x04;
    }
    else if (auto_task > DAYS_2 && auto_task <= DAYS_3)
    {
        PRINTLN("Func: handle_auto_tasks()::rpi_cmd_new_take_photo");
        memcpy(command_data_g.packet, rpi_cmd_new_take_photo, 5); // 0x5500010004
        mission = 0x0f;
    }
    else if (auto_task > DAYS_3 && auto_task <= DAYS_4)
    {
        PRINTLN("Func: handle_auto_tasks()::rpi_cmd_sit");
        memcpy(command_data_g.packet, rpi_cmd_sit, 5); // 0x5500010004
        mission = 0x05;
    }
    else if (auto_task > DAYS_4 && auto_task <= DAYS_5)
    {
        PRINTLN("Func: handle_auto_tasks()::rpi_cmd_rwcs");
        memcpy(command_data_g.packet, rpi_cmd_rwcs, 5); // 0x5500010004
        mission = 0x07;
    }
    else if (auto_task > DAYS_5 && auto_task <= DAYS_6)
    {
        PRINTLN("Func: handle_auto_tasks()::rpi_cmd_seek_laser");
        memcpy(command_data_g.packet, rpi_cmd_seek_laser, 5); // 0x5500010004
        mission = 0x06;
    }
    else if (auto_task > DAYS_6 && auto_task <= WEEK_1)
    {
#if RPI_ENABLE
        PRINTLN("Func: handle_auto_tasks()::Last Mission");
        uint16_t mission = fs_get_misson_index();
        uint16_t file_index = 0x01;
        uint8_t message_len = 0x32;
        uint8_t radio = 0x00; // 433
        prepare_and_send_ld_packet(mission, file_index, message_len, radio);
#endif
    } 
    else if (auto_task > WEEKS_4)
    {
        PRINTLN("Func: handle_auto_tasks()");
        // Reser last_auto_task after a month
        last_auto_task = millis();
    }

    return mission;
}

/* ============== */
/* Handle Tasks   */
/* ============== */
void handle_tasks()
{
    PRINTLN("Func: handle_tasks()");

    if (millis() - last_save_oper_half_days > HALF_DAY)
    {
        last_save_oper_half_days = millis();
        uint8_t error = 0;

        if (sdcard_is_on)
        {
#if SD_ENABLE
            error = increase_operation_half_days_file();
#endif
        }

        if (error || !sdcard_is_on || save_to_flash)
        {
            if (flash_is_on)
            {
#if TNSYFS_ENABLE
                error = fs_increase_operation_half_days_file();
#endif
            }
        }

        last_ranging_24 = 0L;
    }

#if RF_433_ENABLE
    // return to default radio after 1 day
    if (millis() - change_radio_lora_433_setting_timer > DAY_1 && change_radio_lora_433_setting_timer)
    {
        change_radio_lora_433_setting_timer = 0;
        modem_lora_433_setup();
    }

    // return to default radio after 1 day
    if (millis() - change_radio_fsk_433_setting_timer > DAY_1 && change_radio_fsk_433_setting_timer)
    {
        change_radio_fsk_433_setting_timer = 0;
        modem_fsk_433_setup();
    }
#endif

#if RF_24_ENABLE
    if (millis() - change_radio_lora_24_setting_timer > DAY_1 && change_radio_lora_24_setting_timer)
    {
        change_radio_lora_24_setting_timer = 0;
        modem_lora_24_setup();
    }
#endif

    if (!in_mission() && sat_state >= sat_med_power)
    {
        uint8_t mission = handle_auto_tasks();
        if (mission > 0)
        {
#if RPI_ENABLE
            rpi1_turn_on();
            rpi1_command_noack_flag = true;
#endif
        }
    }

#if RPI_ENABLE
    // Check if RPI is ready to send data
    if (rpi1_is_on)
    {
        if (rpi1_command_noack_flag)
        {
            if (rpi1_command_tries < RPI_COMMAND_TRIES) // add tries. if tries > x, then stop trying.
            {
                PRINTLN("RPI: rpi1_command_noack_flag is true");
                activate_command(&command_data_g);
                rpi1_command_tries++;
                PRINT("RPI: rpi1_command_tries:\t");
                PRINTLN(rpi1_command_tries);
            }
            else
            {
                PRINTLN("RPI: Turn off RPI via FAT");
                rpi1_turn_off();
                // reset flags
                rpi1_command_noack_flag = false;
                rpi_task_completed_flag = false;
                rpi1_command_tries = 0;
            }
        }
        else
        {
            PRINTLN("RPI: rpi1_command_noack_flag is false");
            unsigned long time_on = (loop_start_millis > rpi1_is_on) ? loop_start_millis - rpi1_is_on : rpi1_is_on - loop_start_millis; // if start in the same loop then this will be minus.
            // PRINTLN(time_on);
            PRINT("RPI: RPI_1 Is On: ");
            PRINT(time_on / SEC_1);
            PRINTLN(" secs");

            // if rpi is on, check status
            check_rpi_status(rpi1_serial);

            // TODO: Remove this comment
            if (time_on >= MINUTES_3 && time_on < MINUTES_4 || rpi_task_completed_flag)
            {
                PRINTLN("RPI: Sending halt command");
                // command_data_t shoutdown_cmd_g;
                memset(shoutdown_cmd_g.packet, 0x00, COMMAND_PACKET_LENGTH);
                shoutdown_cmd_g.cmd_code = CMD_RPI_1_COMMAND;
                shoutdown_cmd_g.cmd_type = cmd_type_param;
                shoutdown_cmd_g.cmd_size = 1;
                shoutdown_cmd_g.cmd_payload[0] = RPI_CMD_SHUT_DOWN;
                int commandStatus = activate_command(&shoutdown_cmd_g);
                rpi_task_completed_flag = false;
                mission_rpi_flag = false;
            }
            else if (time_on >= MINUTES_4)
            {
                PRINTLN("RPI: Turn off RPI via FAT");
                rpi1_command_noack_flag = false;
                rpi_task_completed_flag = false;
                rpi1_command_tries = 0;
                rpi1_turn_off();
            }
        }
    }
#endif

#if RPI_ENABLE
    // If should turn rpi with dealay
    if (should_turn_rpi1_delay_flag)
    {
        if (millis() - turn_rpi1_delay > turn_rpi1_msec)
        {
            // Turn on RPI
            rpi1_turn_on();
            rpi1_command_noack_flag = true;
            memcpy(command_data_g.packet, command_data_rpi1_g.packet, COMMAND_HEADER_LENGTH + command_data_rpi1_g.cmd_size);
            // sat_state = sat_mission;
            should_turn_rpi1_delay_flag = false;
        }
    }
#endif

    // If should echo msg with delay is on, then wait.
    if (should_echo_msg_delay_flag)
    {
        if (millis() - start_echo_msg_delay > echo_msg_delay_msec)
        {
            // Execute echo message
            should_echo_msg_delay_flag = false;
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

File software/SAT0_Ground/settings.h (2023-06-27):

/**
    @file setting.h
    @brief Header file for SATLLA0 GS.

    This file contains settings and constant for the SATLLA0 GS.

    Copyright (C) 2023 @author Rony Ronen

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
    You should have received a copy of the GNU General Public License
    along with this program.  If not, see <https://www.gnu.org/licenses/>.
*/

#include <SPI.h>
#include <RingBufCPP.h>
#include <TinyGPS++.h>
#include <ArduinoJson.h>
#include <Wire.h>

#define LOCAL_ADDRESS 0xE0
byte local_address = LOCAL_ADDRESS; // default gs address

const char DATE_[] = (__DATE__ "");
const char TIME_[] = (__TIME__ "");
char firmware_version[14 + 1] = {0};

#define BOARD_HELTEC 0
#define BOARD_TEENSY 1
#define BOARD_T_BEAM 2
#define BOARD_T_3V16 3

#define DEVCIE BOARD_HELTEC // 0 : HELTEC, 1: Teensy, 2: TTGO T-BEAM, 3: TTGO T_3 V1.6

#if (DEVCIE == BOARD_HELTEC)    // Heltec
#define GPS_ENABLE 0            // 0=Off, 1=On, 2 : Serial
#define LCD_SSD 0               // 0=Off, 1=On
#define AXP20_ENABLE 0          // 0=Off, 1=On
#define LORA_E22_ENABLE 0       // 0=Off, 1=On
#define LORA_SX126X_ENABLE 0    // 0=Off, 1=On
#define LORA_SX1262_ENABLE 0    // 0=Off, 1=On
#define LORA_SX1278_ENABLE 0    // 0=Off, 1=On
#define LORA_SX128X_ENABLE 1    // 0=Off, 1=On <-
#define LORA_SX1280_ENABLE 0    // 0=Off, 1=On
#define LORA_RL_SX1278_ENABLE 1 // 0=Off, 1=On <-
#define EEPROM_ENABLE 1         // 0=Off, 1=On
#define WIFI_ENABLE 0           // 0=Off, 1=On
#define DRIVE_ENABLE 0          // 0=Off, 1=On
#define FIREBASE_ENABLE 0       // 0=Off, 1=On
#define OTA_ENABLE 0            // 0=Off, 1=On
#define TELEGRAM_ENABLE 0       // 0=Off, 1=On
#define TELEGRAM_BOT_ENABLE 0   // 0=Off, 1=On
#define TELEGRAM_CH_ENABLE 0    // 0=Off, 1=On
#define TLE_ENABLE 0            // 0=Off, 1=On
#elif (DEVICE == BOARD_TEENSY)  // Teensy
#define GPS_ENABLE 0            // 0=Off, 1=On, 2 : Serial
#define LCD_SSD 0               // 0=Off, 1=On
#define AXP20_ENABLE 0          // 0=Off, 1=On
#define LORA_SX126X_ENABLE 0    // 0=Off, 1=On
#define LORA_SX1262_ENABLE 0    // 0=Off, 1=On
#define LORA_SX1278_ENABLE 0    // 0=Off, 1=On
#define LORA_SX128X_ENABLE 1    // 0=Off, 1=On
#define LORA_SX1280_ENABLE 0    // 0=Off, 1=On
#define LORA_RL_SX1278_ENABLE 1 // 0=Off, 1=On <-
#define EEPROM_ENABLE 1         // 0=Off, 1=On
#define WIFI_ENABLE 0           // 0=Off, 1=On
#define DRIVE_ENABLE 0          // 0=Off, 1=On
#define FIREBASE_ENABLE 1       // 0=Off, 1=On
#define OTA_ENABLE 1            // 0=Off, 1=On
#define TELEGRAM_ENABLE 1       // 0=Off, 1=On
#define TELEGRAM_CH_ENABLE 0    // 0=Off, 1=On
#define TLE_ENABLE 0            // 0=Off, 1=On
#elif (DEVCIE == BOARD_T_BEAM)  // TTGO T-BEAM
#define TTGO_VER 1              // 0 : v07, 1 : v1.1 - Control the GPS pins
#define GPS_ENABLE 1            // 0=Off, 1=On, 2 : Serial
#define AXP20_ENABLE 1          // 0=Off, 1=On
#define LCD_SSD 0               // 0=Off, 1=On
#define LORA_SX126X_ENABLE 0    // 0=Off, 1=On
#define LORA_SX1262_ENABLE 0    // 0=Off, 1=On
#define LORA_SX1278_ENABLE 0    // 0=Off, 1=On
#define LORA_SX128X_ENABLE 1    // 0=Off, 1=On
#define LORA_SX1280_ENABLE 0    // 0=Off, 1=On
#define LORA_RL_SX1278_ENABLE 1 // 0=Off, 1=On <-
#define EEPROM_ENABLE 1         // 0=Off, 1=On
#define WIFI_ENABLE 1           // 0=Off, 1=On
#define DRIVE_ENABLE 0          // 0=Off, 1=On
#define FIREBASE_ENABLE 1       // 0=Off, 1=On
#define OTA_ENABLE 1            // 0=Off, 1=On
#define TELEGRAM_ENABLE 1       // 0=Off, 1=On
#define TELEGRAM_BOT_ENABLE 0   // 0=Off, 1=On
#define TELEGRAM_CH_ENABLE 0    // 0=Off, 1=On
#define TLE_ENABLE 1            // 0=Off, 1=On
#else                           // BOARD_T_3V16                        // TTGO T3_V1.6
#define GPS_ENABLE 0            // 0=Off, 1=On, 2 : Serial
#define AXP20_ENABLE 0          // 0=Off, 1=On
#define LCD_SSD 1               // 0=Off, 1=On
#define LORA_SX126X_ENABLE 0    // 0=Off, 1=On
#define LORA_SX1262_ENABLE 0    // 0=Off, 1=On
#define LORA_SX1278_ENABLE 0    // 0=Off, 1=On
#define LORA_SX128X_ENABLE 0    // 0=Off, 1=On
#define LORA_SX1280_ENABLE 0    // 0=Off, 1=On
#define LORA_RL_SX1278_ENABLE 1 // 0=Off, 1=On <-
#define EEPROM_ENABLE 1         // 0=Off, 1=On
#define WIFI_ENABLE 1           // 0=Off, 1=On
#define DRIVE_ENABLE 0          // 0=Off, 1=On
#define FIREBASE_ENABLE 0       // 0=Off, 1=On
#define OTA_ENABLE 0            // 0=Off, 1=On
#define TELEGRAM_ENABLE 1       // 0=Off, 1=On
#define TELEGRAM_CH_ENABLE 0    // 0=Off, 1=On
#define TLE_ENABLE 1            // 0=Off, 1=On
#endif

#define RF_433_ENABLE (LORA_RL_SX1278_ENABLE | LORA_SX126X_ENABLE | LORA_SX1262_ENABLE | LORA_SX1278_ENABLE)
#define RF_24_ENABLE (LORA_SX128X_ENABLE | LORA_SX1280_ENABLE)

#include "debug.h"
#include "data_struct.h"
#include "global_define.h"
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

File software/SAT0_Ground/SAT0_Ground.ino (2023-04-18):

/**
    @file SAT0_Ground.ino
    @brief Master file for SATLLA0 Ground Station.
    Board: Teensy/Heltec32

    This file contains the main and setup functions for the SATLLA0 GS.

    Copyright (C) 2023 @author Rony Ronen

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
    You should have received a copy of the GNU General Public License
    along with this program.  If not, see <https://www.gnu.org/licenses/>.
*/

#define programversion "SATLLA0-GS"
#define Serial_Monitor_Baud 115200

#include "settings.h"

/* ============ */
/* Logo         */
/* ============ */

void logo()
{
#if LCD_SSD
    lcd.clear();
    lcd.drawXbm(0, 5, logo_width, logo_height, logo_bits);
    lcd.display();
    delay(SECS_2);
#endif
}

/* ============ */
/* Setup        */
/* ============ */

void setup()
{
    Serial.begin(Serial_Monitor_Baud);
    delay(HALF_SEC);
    PRINTLN("Setup Started");

    PRINTLN();
    PRINT(__TIME__);
    PRINT(F(" "));
    PRINTLN(__DATE__);
    PRINTLN(programversion);
    PRINTLN();

    get_date(DATE_, buffer_g);
    memcpy(firmware_version, buffer_g, 8);
    get_time(TIME_, buffer_g);
    memcpy(firmware_version + 8, buffer_g, 6);
    PRINT("FIRMWARE_VERSION:\t");
    PRINTLN(firmware_version);
    
#if LCD_SSD
    Wire.begin(OLED_SDA, OLED_SCL);
#endif

#if (DEVCIE == 1)   // Teensy
    SPI.setSCK(14); // For teensy
    SPI.begin();
#else
    SPI.begin(SCK, MISO, MOSI, NSS);
#endif

#if LCD_SSD
    // OLED
    pinMode(OLED_R, OUTPUT);
    digitalWrite(OLED_R, LOW); // set GPIO16 low to reset OLED
    delay(50);
    digitalWrite(OLED_R, HIGH); // while OLED is running, must set GPIO16 in high

    lcd.init();
    lcd.flipScreenVertically();
    lcd.clear();
    lcd.display();

    logo();

    lcd.clear();
    lcd.setTextAlignment(TEXT_ALIGN_CENTER);
    lcd.setFont(ArialMT_Plain_10);
    lcd.drawString(64, 0, "SATLLA0 GS Start");
    lcd.drawString(64, 10, String(local_address, HEX));
    lcd.drawString(64, 20, firmware_version);
    lcd.display();

    lcd.setTextAlignment(TEXT_ALIGN_LEFT);
    // lcd.setFont(DejaVu_Sans_10);
#endif

#if AXP20_ENABLE
    axp20_setup();
    axp20_raw_print();
#endif

#if EEPROM_ENABLE
    eeprom_setup();
    load_settings();
    print_settings();
#endif

#if WIFI_ENABLE
    wifi_setup();

#if OTA_ENABLE
    arduinoota_setup();
#endif

#if TELEGRAM_ENABLE
    tlg_setup();

    publish_to_tlg_message("Station was restarted!.");
#endif

#if TELEGRAM_BOT_ENABLE
    tlgrelay_setup();
#endif

#if FIREBASE_ENABLE
    firebase_setup();
#endif

#if TLE_ENABLE
    tle_setup();
#endif

#endif

    // LoRa 433 Setup
#if RF_433_ENABLE
    lora_433_setup();
    // modem_fsk_433_setup(); // Need to set FSK as well
#endif

#if RF_24_ENABLE
    // LoRa 2.4 Setup
    lora_24_setup();
#endif

#if GPS_ENABLE
    gps_setup();
#endif

    button_setup();

#if TRK_ENABLE
    trk_setup();
    find_north();
#endif

#if LCD_SSD
    lcd.drawString(0, 20, "Heltec.LoRa 433 success!");
    lcd.drawString(0, 30, "Heltec.LoRa 2.4 success!");
    lcd.drawString(0, 40, "Setup Completed");
    lcd.display();
#endif

    PRINTLN("Setup Completed");
}

/* ============ */
/* Loop         */
/* ============ */

void loop()
{
    // if restart requested wait 5 secs and restart
    if (restart_requested_flag && millis() - restart_requested_flag > SECS_10)
    {
        CPU_RESTART;
    }

    if (Serial.available() > 0)
    {
        serial_event();
    }

    if (button_pressed_flag)
    {
        PRINTLN("Flag: button_pressed_flag");
        if (digitalRead(BTN_PRG_PIN) == HIGH)
        {
            // PRINTLN("Flag: HIGH");
            button_setup();
        }
        else
        {
            // PRINTLN("Flag: LOW");
        }
    }

#if GPS_ENABLE
    if (gs_gps_enable)
    {
        gps_read();
        gps_info();
    }
#endif

#if RF_433_ENABLE
    if (received_433_flag)
    {
        received_433_flag = false;
        delay(10);
#if LORA_SX127X_ENABLE
        on_receive_433();
#endif
        handle_433_message();
    }
#endif

#if RF_24_ENABLE
    if (received_24_flag)
    {
        received_24_flag = false;
        delay(10);
        on_receive_24();
        handle_24_message();
        setup_lora_24_rx();
    }
#endif

#if WIFI_ENABLE

#if TELEGRAM_BOT_ENABLE
    if (millis() - tlgrelay_read_millis > tlg_read_threshold)
    {
        tlgrelay_read();
        tlgrelay_read_millis = millis();
    }
#endif

#if TELEGRAM_ENABLE
    if (millis() - tlg_read_millis > tlg_read_threshold)
    {
        tlg_read();
        tlg_read_millis = millis();
    }
#endif

#if TLE_ENABLE
    if (millis() - tle_read_millis > tle_read_threshold)
    {
        tle_loop();
        tle_read_millis = millis();
    }

    // update TLE each day
    if (millis() - tle_updated_millis > tle_updated_threshold)
    {
        tle_updated_millis = millis();
        update_TLE();
        switch_next_sat();
    }
#if TRK_ENABLE
    trk_loop();
#endif
#endif

#if OTA_ENABLE
    arduinoota_handle();
#endif
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

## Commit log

2022-12-15 Improve README, Fix License. Remove SIT.
    [TakePicSmart.py, controller.py, define.py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]
2022-12-17 Add docs.
    [left-right-holders.SLDPRT, left_panel.stl, pod_box.stl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]
2022-12-26 Dev (#8)
    * Fix figure
    * Fix figure
    * Fix figure path
    * Update paper.md
    * Update paper.md
    * Update paper.md
    * Update paper.md
    * Update paper.md
    * Add files via upload
    * Fix figure path
    * Fix figure path
    * Fix figure path
    * Fix figure path
    * Update paper.md
    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
    [controller.py, utils.py]
2023-01-07 added setup guide for OBC + fixed sat.service
    [config.txt]
2023-01-29 Added PCB files
    [BOM_Satlla_4_Back_side_2023-01-29.csv, BOM_Satlla_4_Front_side_2023-01-29.csv, BOM_Satlla_4_Main_Board_2023-01-26.csv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]
2023-02-12 #14 Repository documentation and structure
    [BOM_Satlla_4_Back_side_2023-01-29.csv, BOM_Satlla_4_Front_side_2023-01-29.csv, BOM_Satlla_4_Main_Board_2023-01-26.csv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]
2023-05-21 # Change BOARD_T_BEAM LORA_433_RST_PIN 23
2023-05-21 # Change BOARD_T_BEAM LORA_433_RST_PIN changed
2023-06-07 Add SATLLA-0 EVM Board and few changes to support Teensy32
2023-06-18 Surround parse_setting() with EEPROM. Fix typo. Add TEENSY3.2 option.
    [Serial_Event.ino, settings.h]
2023-06-25 Update PINs for the Teensy3.2 (EVM)
2023-06-27 Dev (#37)
    * #29 Include link to the repository in the paper (#30)
    * # Change BOARD_T_BEAM LORA_433_RST_PIN 23
    * Add SATLLA-0 EVM Board and few changes to support Teensy32
    * Broken link on README.
    * Surround parse_setting() with EEPROM. Fix typo. Add TEENSY3.2 option.
    * Paper review issues #35
    * Update PINs for the Teensy3.2 (EVM)
    * Update LoRa_RL_SX1278.ino
    [GPS_Airborne.ino, LoRa_RL_SX1278.ino, SAT0_Master.ino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]

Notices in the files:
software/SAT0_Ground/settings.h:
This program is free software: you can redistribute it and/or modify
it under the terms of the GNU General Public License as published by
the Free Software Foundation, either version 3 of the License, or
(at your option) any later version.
